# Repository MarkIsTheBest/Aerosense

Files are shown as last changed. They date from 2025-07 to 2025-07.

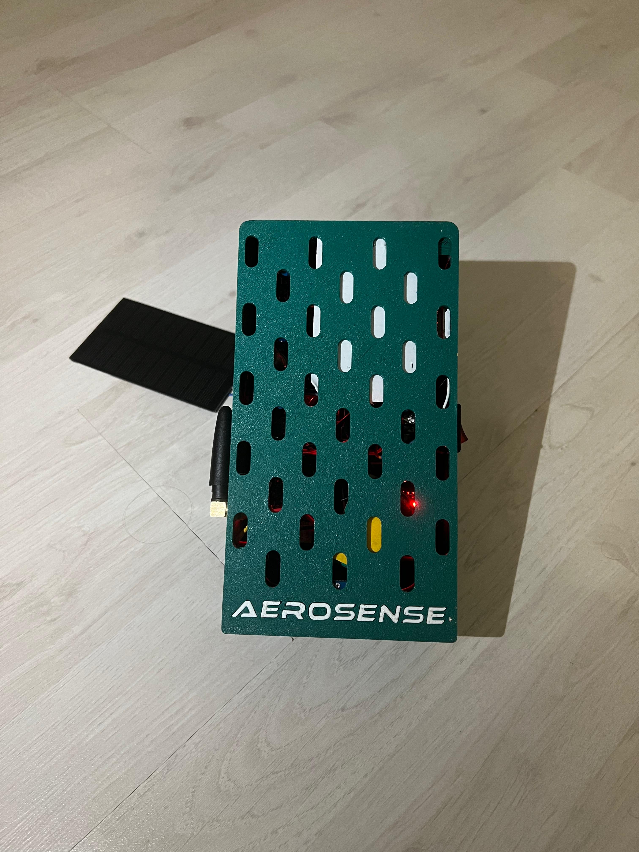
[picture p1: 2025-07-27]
Photos/Aerosense-7.jpg

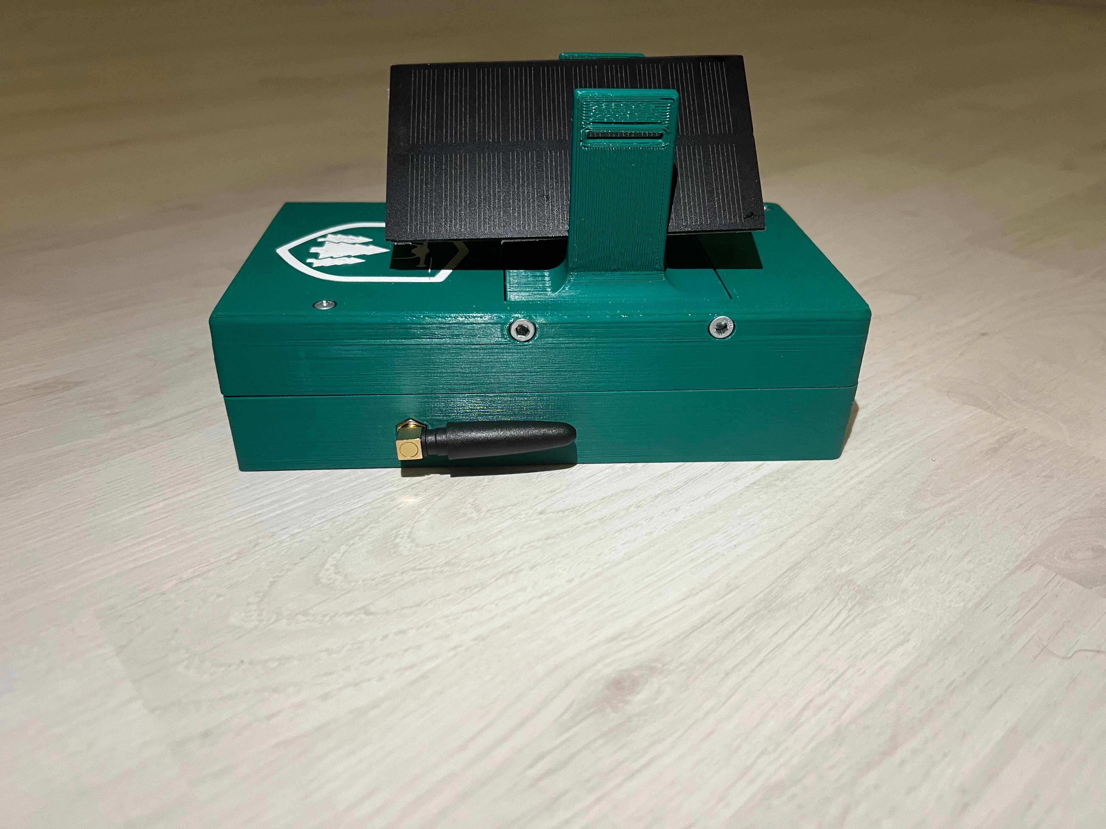
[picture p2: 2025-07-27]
Photos/Aerosense-8.jpg

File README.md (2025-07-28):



#### *Statie Meteo Mobila Autonoma, pentru culegerea datelor meteorologice, oricand si oriune.*

---

> [!NOTE]
> Acest ``README.md`` este strict dedicat partii technice al acestui proiect, pentru detalii mai generale, te rog visualizeaza prezentarea powerpoint, sau daca ai mai mult timp de citit, poti visualiza chiar si documentatia in intregime!

---

### Ierarhie pagina Github:
La ``Aerosense/Scripts/Drone.ino`` se gaseste codul Microcontroller-ului, acesta gestioneaza atat senzorii,
 cat si trimiterea lor pe webserver prin intermediului unei cartele SIM, iar simultan datele inregistrate sunt salvate
 pe o cartela MicroSD.

La ``Aerosense/Scripts/Webserver/`` se gasesc script-urile pentru Webserver, acestea includ:
- ``server.js`` (functionalitatea principala a server-ului prin intermediul Node.js)
- ``index.html`` (codul de baza a front-end-ului)
- ``style.css`` (stilistica front-end)

La ``Aerosense/3DModels/`` se gaseste modelul 3d al carcasei printate, care faciliteaza locuinta intregului sistem. Acest model se gaseste in mai multe format-uri pentru a usura uzul acestora. (Fusion360)

La ``Aerosense/Datasheets/`` se gasesc documente specifice a diverselor parti furnizate extern al sistemului nostru, cum ar fi de exemplu: baterie ce noi o folosim.

La ``Aerosense/Documentation/`` se gaseste atat documentatia cat si o prezentare powerpoint, pentru a usura intelegerea proiectului/sistemului, fiind scrisa la un mod mai general decat acest ``README.md`` care este strict technic:
- ``Aerosense Documentation.pdf`` (asa numita documentatie de 12 pagini)
- ``Aerosense Presentation.pptx`` (prezentare powerpoint generala)

La ``Aerosense/Photos/`` se gasesc diverse poze, capturand infatisarea sistemului, atat pe dinafara cat si pe dinauntru. Aceste poze va pot ajuta in vizualizaera sistemului.

La ``Aerosense/Schematics/`` se gaseste schematica circuitului electric facut in KiCad. Aceasta schematica nu face posibila doar visualizarea conexiuniilor electrice intre diferitii senzori, ci si a sistemului de alimentare. Urmarind aceasta schematica, proiectul poate fii facut mult mai mic prin intermediul, unui PCB presonalizat.

La ``Aerosense/Identity/`` se gaseste identitatea produsului, adica logo-ul si titlul acestuia, ambele pot fii gasite si pe carcasa sistemului.

-----

# Hardware:

### Componentele electronice de baza:
 1. #### Circuit Principal:
    * Microprocessor | Arduino Nano (USB C)
    - Senzor temperatura, presiune si umiditate | BME280
    - Busola/Magnetometru | QMC5883L
    - Senzor analogic de gaz si fum | MQ-7
    - Senzor analogic de oxid de carbon (CO) | MQ-5
    - Modul accelerometru + airoscop | MPU6050
    - Modul cartela SIM GSM + GPRS (+ Antena + SIM orange prepay) | SIM800LV2 EVB 
    - Senzor calitatea aerului | SGP30
    - Modul GPS (+ Antena) | NEO6MV3
    - Modul MicroSD Card (+ MicroSDHD Card 32GB)

2. #### Circuit Alimentare:
   - Acumulator Li-Ion 3.7V (MAX 4.2) 3350mAh | Samsung INR18650-25E
   - Panou Solar 5V 1W | YX-107X61
   - Modul Incarcare solara acumulator 3.7V | MPPT
   - Voltmetru (incarcatura acumulator)
   - Intrerupator (oprirea circuitului)
   - Ridicator de tensiune (3.7V -> 5V) 5A | XL6019
  
### Echipament utilizat:
| Tools | Manufacturer |
| --- | --- |
| `Ciocan de lipit (380C)` | `WCD` |
| `Ciocan de lipid (280C)` | `Dedeman` | 
| `Pistol Termic (380C)` | `WCD` |
| `Cositor SWCU 1/17 227C (fara plumb)` | `Dedeman` |
| `Sursa programabila 161,2W (5.2A)` | `WAPTEK` |
| `Imprimanta 3D Ender 3 V3 KE` | `Creality` |
| `+ Alte scule si unelte gasite` | `Acasa` |

-----

# Software:

### Librarii Folosite:

 1. #### Arduino:
    * ``SoftwareSerial.h`` (pentru a putea folosii oricare pini ca si TX/RX)
    * ``QMC5883LCompass.h`` (pentru gestionarea usoara si eficienta a busolei)
    * ``TinyGPSPlus.h`` (pentru interpretarea datelor primite de la sateliti)
    * ``I2Cdev.h`` (pentru conectarea si usurinta uzual a protocolului I2C)
    * ``MPU6050.h`` (pentru calibrarea si utilizarea eficienta a IMU-ului)
    * ``Wire.h`` (pentru a putea folosi protocolul de transmitere I2C)
    * ``sSense-BMx280I2C.h`` (pentru a banaliza folosirea senzorului ambiental)
    * ``Adafruit_SGP30.h`` (pentru a banaliza folosirea senzorului de calitate a aerului)
      
 2. #### Webserver:
    * ``http`` (pentru a facilita crearea unui server http)
    * ``fs`` (pentru a gestiona fisiere cu Node.js)
    * ``path`` (pentru a gestiona adresele fisierelor)
    * ``mysql2 + promise`` (pentru a efectua conexiunea cu baza de date mySQL)
    * ``leaflet(API)`` (pentru a avea acces la harta lumii)
    * ``gemini(API)`` (pentru a explica datele complicate utilizatorilor "non-experti")

### Baza de Date: MySQL

Pentru a stoca în mod persistent datele primite de la dronă, sistemul utilizează o bază de date ``MySQL``. Serverul ``Node.js`` acționează ca o punte de legătură între microcontroler și baza de date.
Conectarea la Baza de Date: Scriptul ``server.js`` folosește librăria ``mysql2/promise`` pentru a se conecta la serverul ``MySQL``. Detaliile de conectare (host, utilizator, parolă, numele bazei de date) sunt definite în obiectul ``dbConfig``.

#### Primirea și Inserarea Datelor:
1. Când microcontrolerul trimite date printr-o cerere ``POST`` la adresa ``/data``, serverul ``Node.js`` primește aceste informații în format ``JSON``.
2. Serverul adaugă un timestamp exact la momentul recepției pentru a asigura acuratețea temporală.
3. Datele sunt apoi inserate în tabelul ``drone_data`` din baza de date esp32_data folosind o interogare ``SQL`` de tip ``INSERT``. Utilizarea interogărilor parametrizate (cu ?) previne atacurile de tip ``SQL`` injection.
   
#### Livrarea Datelor către Front-End:
1. Pagina web (``index.html``) solicită datele de la server prin intermediul unei cereri ``GET`` la adresa ``/api/data``.
2. Serverul răspunde acestei cereri prin executarea unei interogări ``SQL`` de tip SELECT * FROM drone_data, extrăgând toate înregistrările.
3. Datele extrase sunt trimise către front-end în format JSON, unde sunt apoi folosite pentru a popula graficele și harta ``Leaflet``.

### Software extern utilizat:
| Software Name | Download Link |
|---|---|
| `Arduino IDE` | [`https://www.arduino.cc/en/software/`](https://www.arduino.cc/en/software/) |
| `Visual Studio Code` | [`https://code.visualstudio.com/`](https://code.visualstudio.com/) |
| `Fusion360` | [`https://www.autodesk.com/products/fusion-360/personal`](https://www.autodesk.com/products/fusion-360/personal) |
| `Creality Print` | [`https://www.creality.com/pages/download-software`](https://www.creality.com/pages/download-software) |
| `KiCad` | [`https://www.kicad.org/download/windows/`](https://www.kicad.org/download/windows/) |
| `MySQL` | [`https://www.mysql.com`](https://www.mysql.com) |
| `Gemini Pro AI` | [`https://gemini.google.com/`](https://gemini.google.com/) |
| `Canva` | [`https://www.canva.com/`](https://www.canva.com/) |

-----

## Galerie Foto:

### Placa de baza a sistemului:


### Sistemul de alimentare a placii:


### Schematica completa a sistemului din KiCad:


### Webserver-ul dronei:


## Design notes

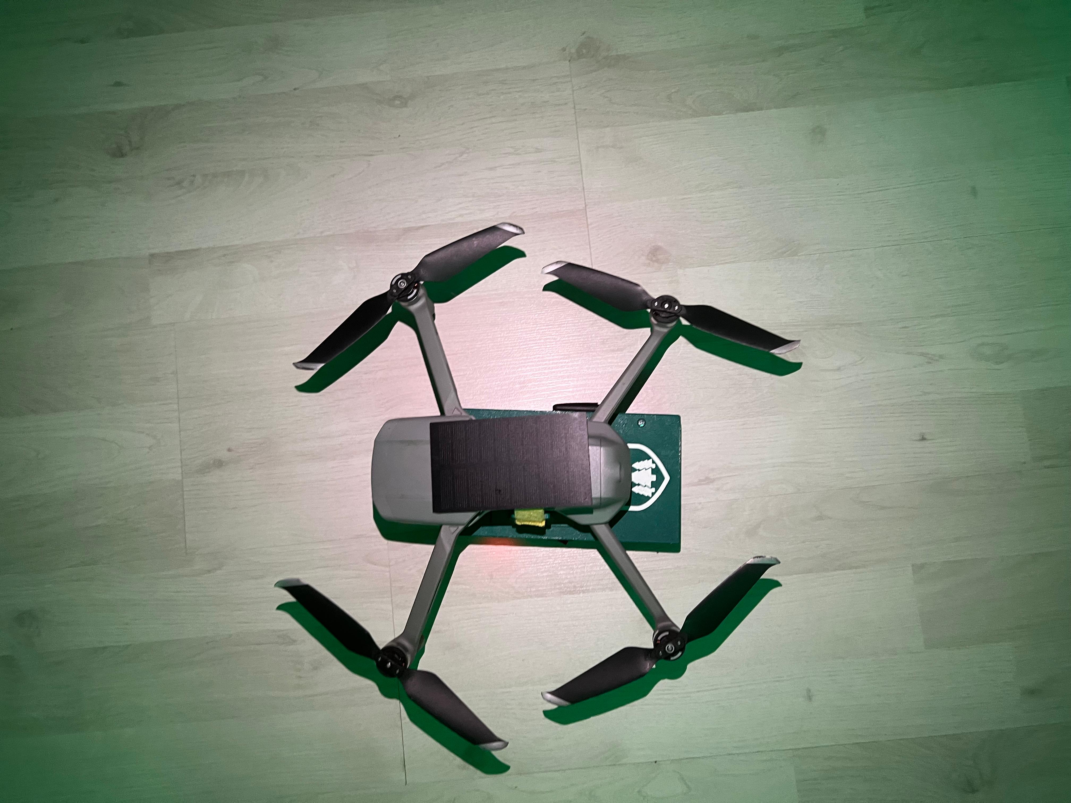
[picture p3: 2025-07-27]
Photos/Aerosense-5.jpg

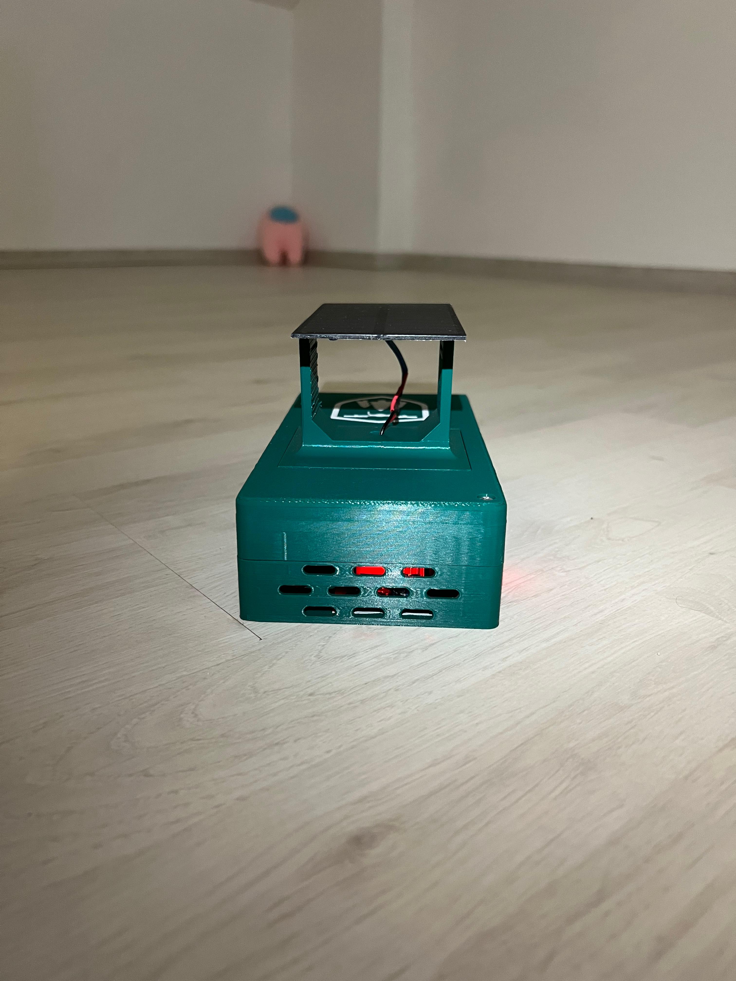
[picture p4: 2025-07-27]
Photos/Aerosense-2.jpg

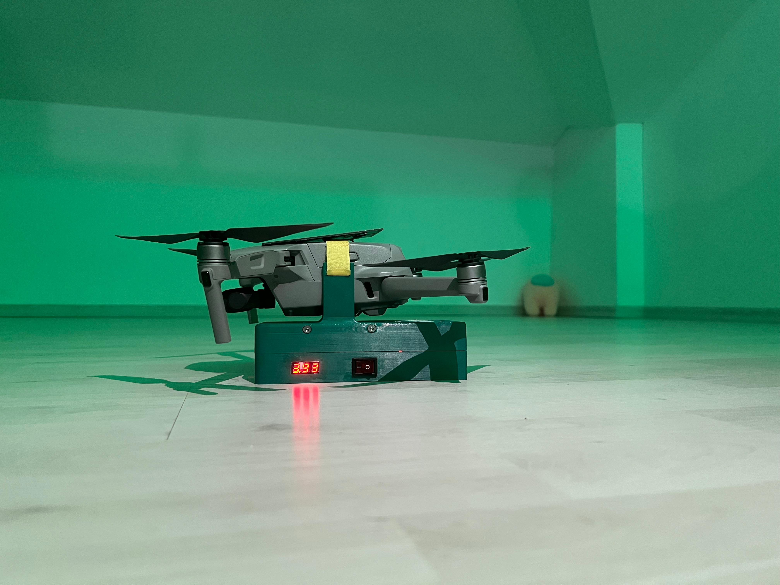
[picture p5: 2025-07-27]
Photos/Aerosense-4.jpg

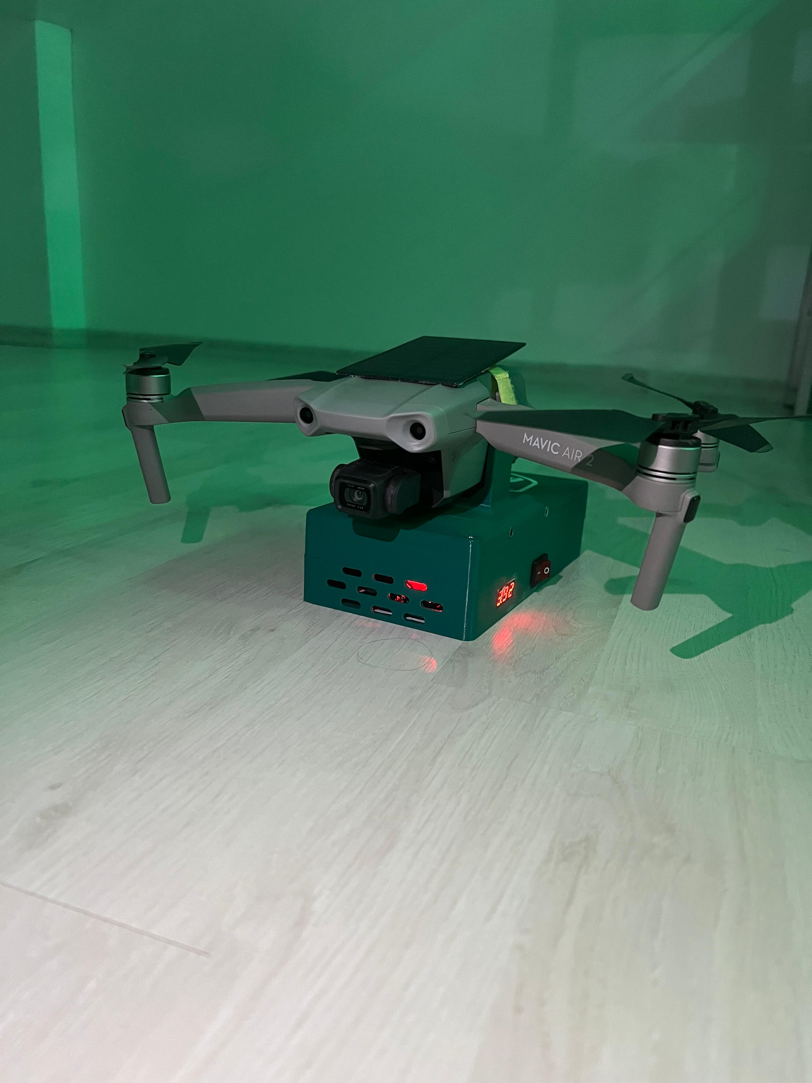
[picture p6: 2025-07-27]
Photos/Aerosense-1.jpg

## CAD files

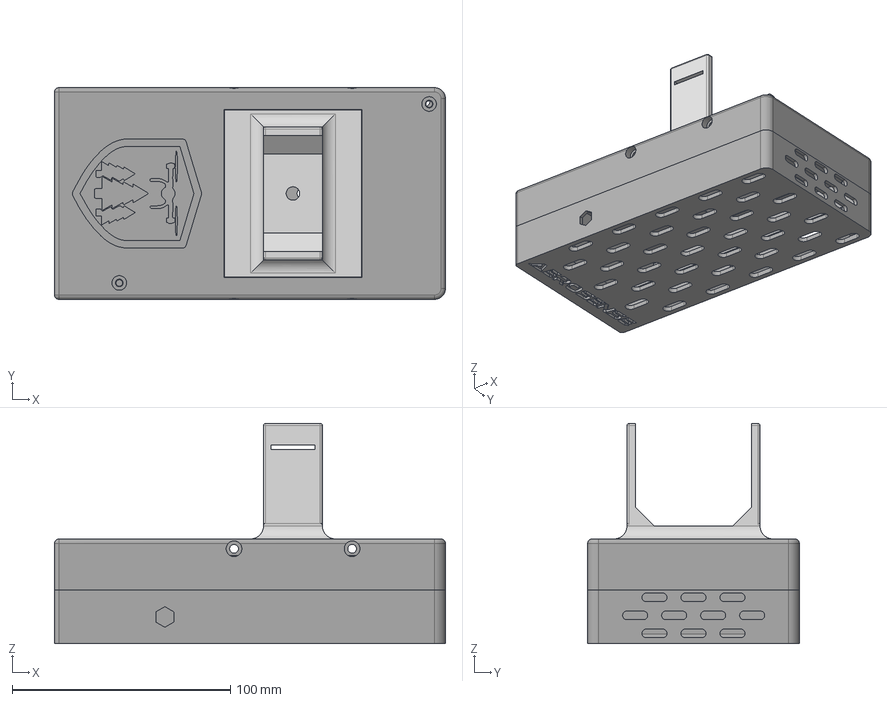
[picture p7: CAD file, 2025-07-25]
3DModels/Housing.step
179.2 x 97.0 x 101.0 mm
sketch
capac
fund (1)
scris

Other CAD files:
3DModels/Housing.3mf
3DModels/Housing.stl

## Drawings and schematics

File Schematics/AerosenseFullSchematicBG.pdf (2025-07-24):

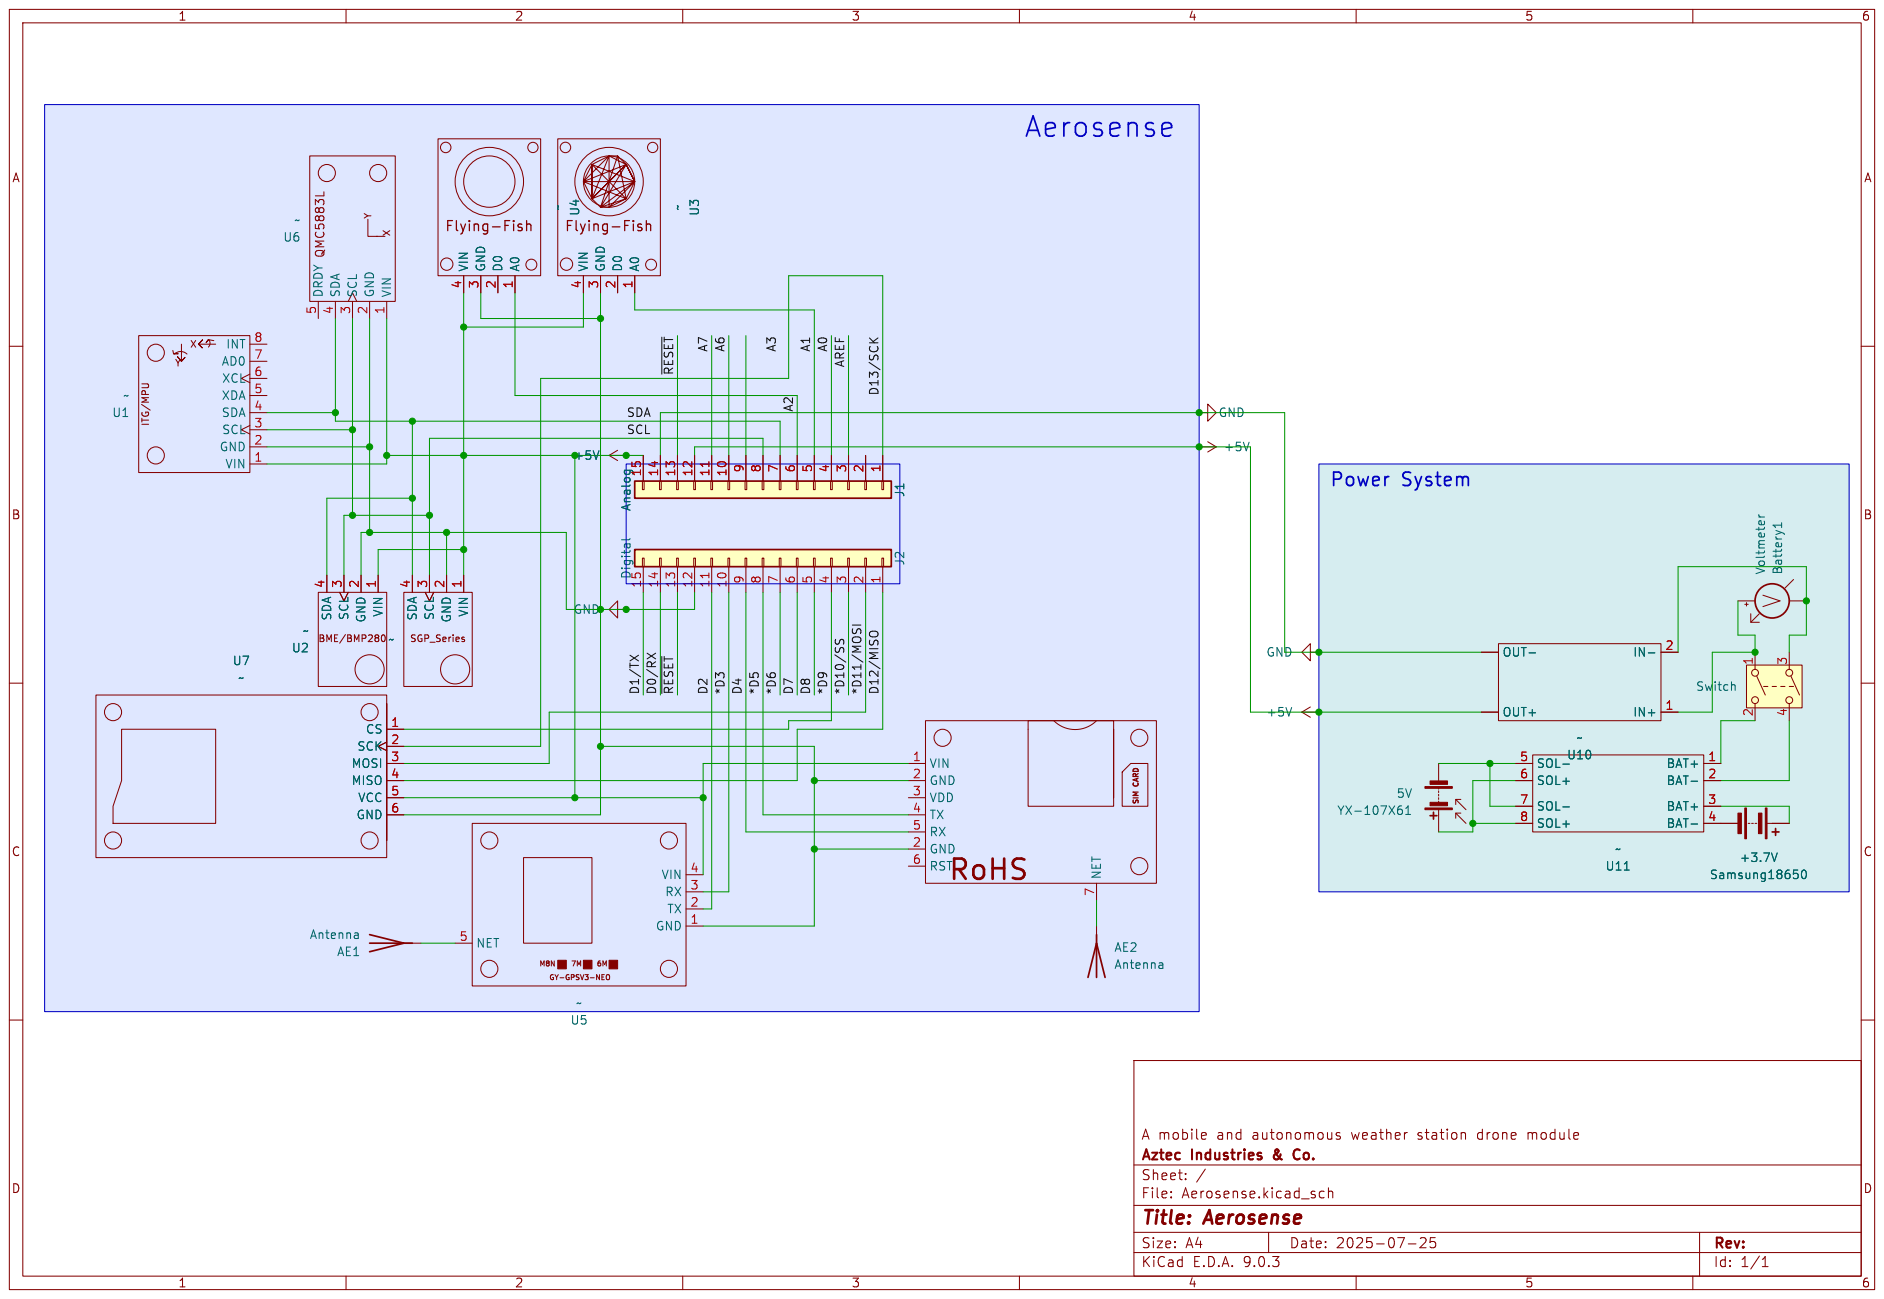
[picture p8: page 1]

4 U7~ CS 1 SCK 2 MOSI 3 MISO 4 VCC 5 GND 6~ VIN

1151413121110 J2 Digital A7 D1/TX D0/RX D2 D4 *D5 *D6 SCL ~{RESET} *D9 *D11/MOSI SDA D8 *D10/SS D12/MISO D13/SCK A2 A0 AREF *D3 D7 ~{RESET} A6A3A1

4 ~ BAT- 4 BAT+ 3 BAT- 2 BAT+ 1 SOL+ 8 SOL- 7 SOL+ 6 SOL- 5 U11~ AE2 Antenna RoHS SIM CARDVIN 1 GND 2 VDD 3 TX 4 RX 5 GND 2 RST 6 NET

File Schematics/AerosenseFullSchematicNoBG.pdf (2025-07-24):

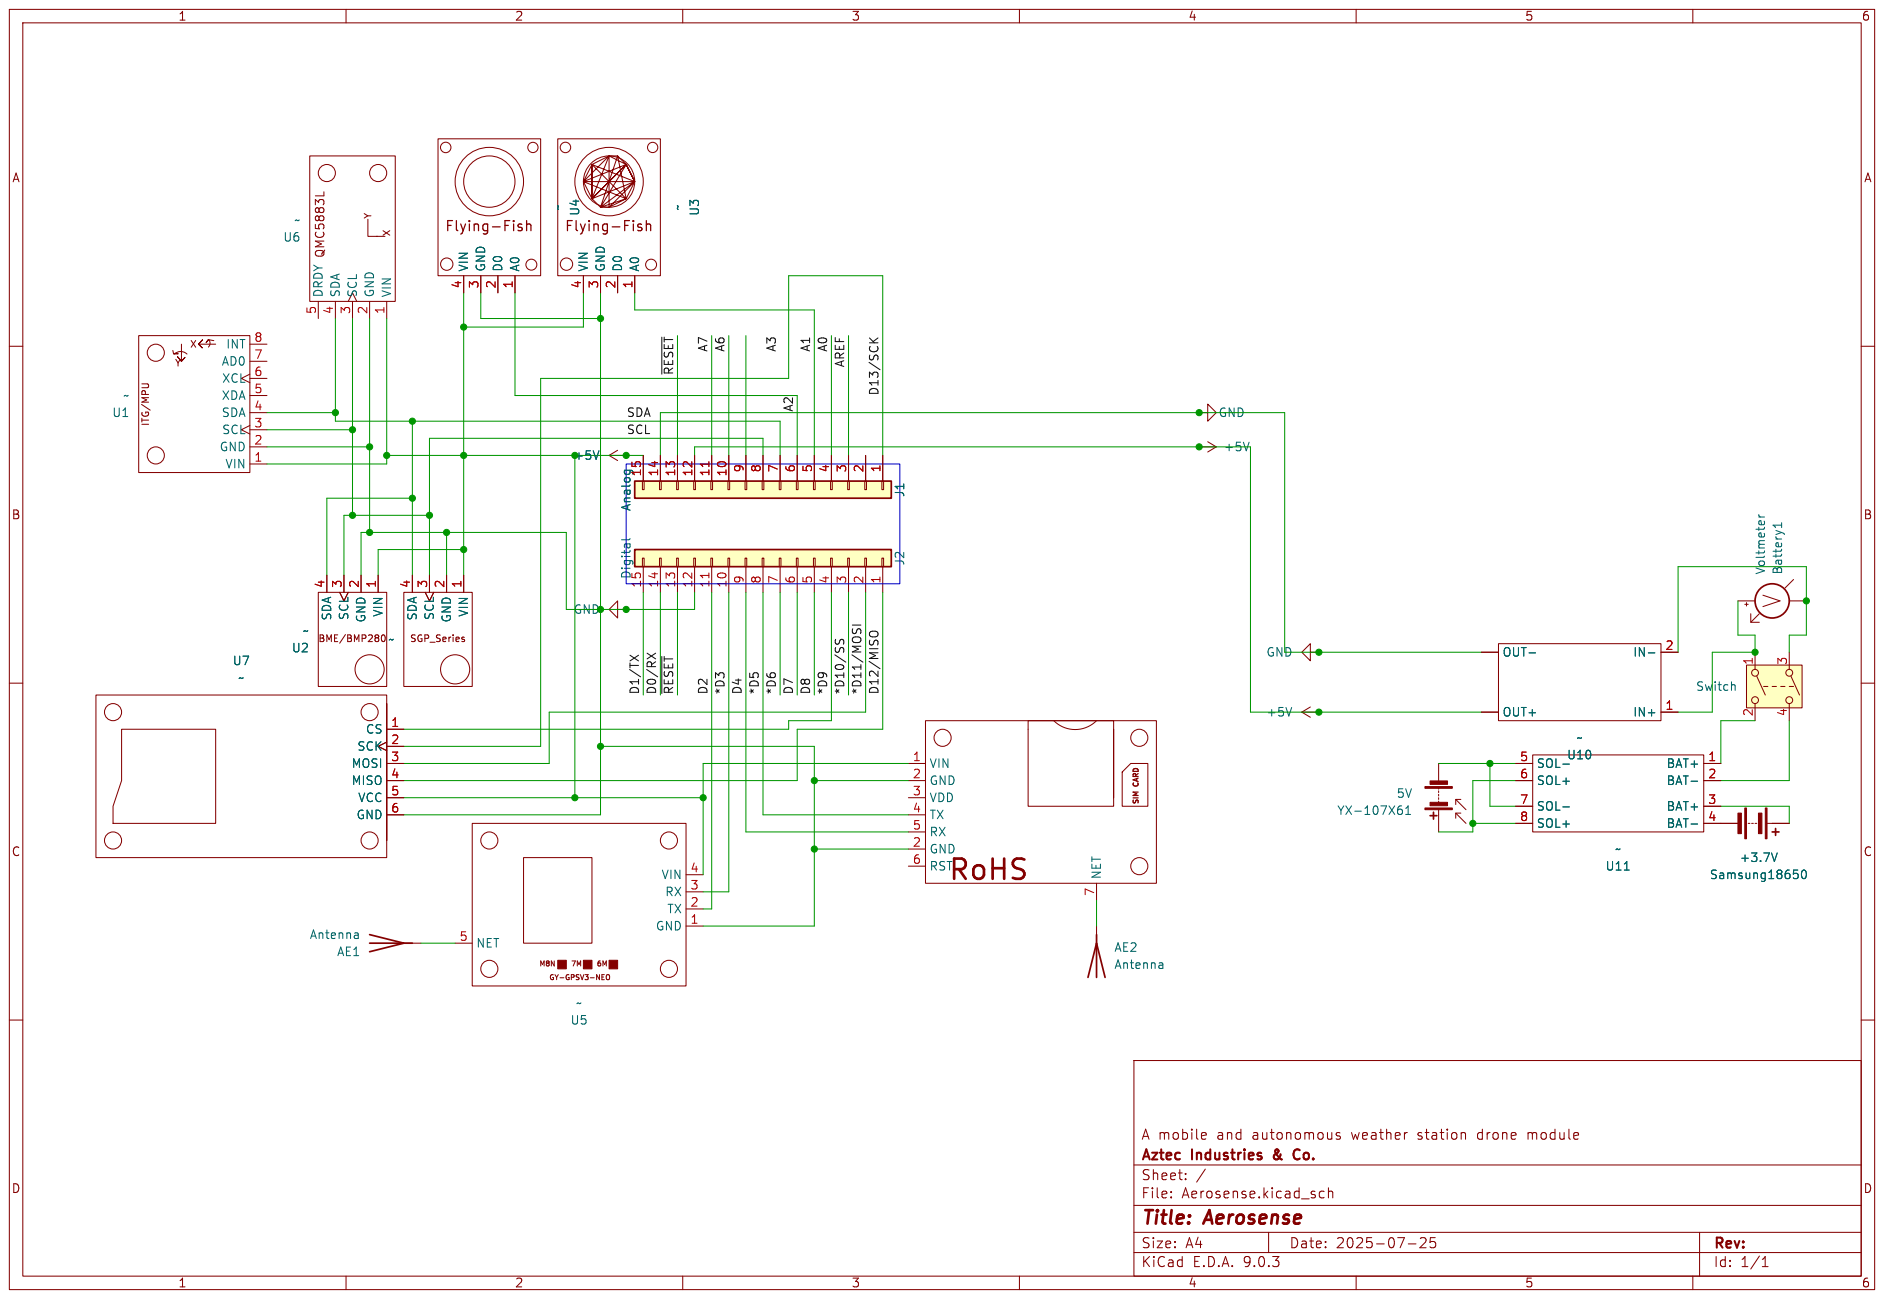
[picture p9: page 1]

4 U7~ CS 1 SCK 2 MOSI 3 MISO 4 VCC 5 GND 6~ VIN

4 ~ BAT- 4 BAT+ 3 BAT- 2 BAT+ 1 SOL+ 8 SOL- 7 SOL+ 6 SOL- 5 U11~ RoHS SIM CARDVIN 1 GND 2 VDD 3 TX 4 RX 5 GND 2 RST 6 NET

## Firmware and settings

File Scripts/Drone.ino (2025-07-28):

#include <SoftwareSerial.h>
#include <QMC5883LCompass.h>
#include <TinyGPSPlus.h>
#include "I2Cdev.h"
#include "MPU6050.h"
#include <Wire.h>
#include <Adafruit_BME280.h>
#include <Adafruit_SGP30.h>

const char APN[] = "net";
const char SERVER_IP[] = "62.231.112.115";
const char SERVER_PORT[] = "25565";

const int SIM800_RX_PIN = 4;
const int SIM800_TX_PIN = 5;
const int GAS_SENSOR_MQ5_PIN = A1;
const int GAS_SENSOR_MQ7_PIN = A2;
const int GPS_RX_PIN = 3;
const int GPS_TX_PIN = 2;
const uint32_t GPS_BAUD = 9600;
const float ACCEL_SCALE_FACTOR = 16384.0;
const float GRAVITY_MS2 = 9.81;

SoftwareSerial sim800l(SIM800_RX_PIN, SIM800_TX_PIN);
QMC5883LCompass compass;
TinyGPSPlus gps;
SoftwareSerial gpsSerial(GPS_RX_PIN, GPS_TX_PIN);
MPU6050 mpu;
Adafruit_BME280 bme; // I2C
Adafruit_SGP30 sgp;

char compassDirection[4];
int gasAnalogValue;
int coAnalogValue;
float gpsLatitude = 0.0;
float gpsLongitude = 0.0;
float gpsAltitude = 0.0;
float gpsSpeed = 0.0;
uint32_t sats = 0;
float accelX, accelY, accelZ;
float temperature, humidity, pressure;
uint16_t tvocLevel, co2Level;

unsigned long lastSendTime = 0;
const long sendInterval = 5000;

void setup() {
    Serial.begin(9600);
    sim800l.begin(9600);
    gpsSerial.begin(GPS_BAUD);

    Wire.begin();
    Wire.setClock(400000);

    Serial.println(F("--- Universal Sensor & GPRS Initializer ---"));
    delay(1000);

    initializeSensors();
    initializeGPRS();

    Serial.println(F("\n--- Setup complete. Starting main loop. ---\n"));
    lastSendTime = millis();
}

void loop() {
    gpsSerial.listen();
    
    while (gpsSerial.available() > 0) {
        gps.encode(gpsSerial.read());
    }

    if (millis() - lastSendTime >= sendInterval) {
        lastSendTime = millis();

        Serial.println(F("\n========================================"));
        Serial.println(F("Interval reached. Reading sensors and sending data..."));

        readAllSensors();
        sendData();

        Serial.println(F("========================================"));
    }
}

void readAllSensors() {
    Serial.println(F("--- Reading all sensor data... ---"));
    if (gps.location.isUpdated()) {
        gpsLatitude = gps.location.lat();
        gpsLongitude = gps.location.lng();
    }
    if (gps.altitude.isUpdated()) gpsAltitude = gps.altitude.meters();
    if (gps.speed.isUpdated()) gpsSpeed = gps.speed.kmph();
    if (gps.satellites.isUpdated()) sats = gps.satellites.value();

    compass.read();
    compass.getDirection(compassDirection, compass.getAzimuth());

    gasAnalogValue = analogRead(GAS_SENSOR_MQ5_PIN);
    coAnalogValue = analogRead(GAS_SENSOR_MQ7_PIN);

    int16_t raw_ax, raw_ay, raw_az;
    mpu.getAcceleration(&raw_ax, &raw_ay, &raw_az);
    accelX = (raw_ax / ACCEL_SCALE_FACTOR) * GRAVITY_MS2;
    accelY = (raw_ay / ACCEL_SCALE_FACTOR) * GRAVITY_MS2;
    accelZ = (raw_az / ACCEL_SCALE_FACTOR) * GRAVITY_MS2;

    temperature = bme.readTemperature();
    humidity = bme.readHumidity();
    pressure = bme.readPressure(); // This returns pressure in Pascals (Pa)
    if (humidity > 0) sgp.setHumidity(getAbsoluteHumidity(temperature, humidity));
    if (sgp.IAQmeasure()) {
        tvocLevel = sgp.TVOC;
        co2Level = sgp.eCO2;
    }
    printData();
}

void sendData() {
    sendHttpPost();
}

void initializeSensors() {
    Serial.println(F("--- Initializing Sensors ---"));
    Serial.print(F("QMC5883L... "));
    compass.init();
    Serial.println(F("Done."));
    Serial.print(F("MPU6050... "));
    mpu.initialize();
    if (mpu.testConnection()) {
        Serial.println(F("OK. Setting offsets..."));
        mpu.setXAccelOffset(1690); mpu.setYAccelOffset(870); mpu.setZAccelOffset(4640);
        mpu.setXGyroOffset(-46); mpu.setYGyroOffset(68); mpu.setZGyroOffset(88);
    } else {
        Serial.println(F("Failed."));
    }
    Serial.print(F("BME280... "));
    if (!bme.begin(0x76)) Serial.println(F("Failed. Check wiring or I2C address!"));
    else Serial.println(F("Done."));
    Serial.print(F("SGP30... "));
    if (!sgp.begin()) Serial.println(F("Failed."));
    else Serial.println(F("Done."));
    Serial.println(F("--- Sensor Initialization Complete ---"));
}

void initializeGPRS() {
    sim800l.listen();
    Serial.println(F("--- Initializing SIM800L Module ---"));
    delay(3000);
    if (!checkModule()) {
        Serial.println(F("FATAL: SIM800L module not responding. Halting."));
        while (1);
    }
    sendATCommand(F("AT+HTTPTERM"), F("OK"), 5000);
    sendATCommand(F("AT+SAPBR=0,1"), F("OK"), 5000);
    setupGPRS();
}

unsigned int countDigits(int number) {
  if (number < 0) return countDigits(-number) + 1;
  if (number < 10) return 1;
  if (number < 100) return 2;
  if (number < 1000) return 3;
  if (number < 10000) return 4;
  return 5;
}

bool expectResponse(const __FlashStringHelper* ack, unsigned int timeout) {
    String response = "";
    response.reserve(64);
    long int startTime = millis();
    bool ackFound = false;
    while ((millis() - startTime) < timeout) {
        while (sim800l.available()) {
            response += (char)sim800l.read();
        }
        if (response.indexOf(ack) != -1) {
            ackFound = true;
            break;
        }
    }
    Serial.print(F("<<< Response: "));
    Serial.println(response);
    return ackFound;
}

bool sendATCommand(const __FlashStringHelper* cmd, const __FlashStringHelper* ack, unsigned int timeout) {
    Serial.print(F(">>> AT: "));
    Serial.println(cmd);
    sim800l.println(cmd);
    return expectResponse(ack, timeout);
}

bool checkModule() {
    return sendATCommand(F("AT"), F("OK"), 2000);
}

void setupGPRS() {
    Serial.println(F("--- Configuring GPRS ---"));
    sendATCommand(F("AT+CREG?"), F("+CREG: 0,1"), 10000);
    sendATCommand(F("AT+CGATT=1"), F("OK"), 5000);
    sim800l.print(F("AT+SAPBR=3,1,\"CONTYPE\",\"GPRS\"\r\n"));
    expectResponse(F("OK"), 2000);
    sim800l.print(F("AT+SAPBR=3,1,\"APN\",\""));
    sim800l.print(APN);
    sim800l.print(F("\"\r\n"));
    expectResponse(F("OK"), 2000);
    sendATCommand(F("AT+SAPBR=1,1"), F("OK"), 20000);
    sendATCommand(F("AT+SAPBR=2,1"), F("+SAPBR:"), 5000);
    Serial.println(F("--- GPRS Configuration Complete ---"));
}

void sendHttpPost() {
    sim800l.listen();
    Serial.println(F("--- Starting HTTP POST ---"));
    if (!sendATCommand(F("AT+HTTPINIT"), F("OK"), 5000)) return;

    sim800l.print(F("AT+HTTPPARA=\"URL\",\"http://"));
    sim800l.print(SERVER_IP);
    sim800l.print(F(":"));
    sim800l.print(SERVER_PORT);
    sim800l.print(F("/data\"\r\n"));
    if (!expectResponse(F("OK"), 2000)) return;

    sendATCommand(F("AT+HTTPPARA=\"CONTENT\",\"application/json\""), F("OK"), 2000);

    char tempBuffer[12];
    int jsonLength = 0;
    jsonLength += strlen_P(PSTR("{\"path\":1,\"timestamp\":\"2025-01-01 00:00:00\",\"longitude\":,\"latitude\":,\"temperature\":,\"humidity\":,\"pressure\":,\"CO2level\":,\"TVOClevel\":,\"imuXaccel\":,\"imuYaccel\":,\"imuZaccel\":,\"COlevel\":,\"Gaslevel\":,\"altitude\":,\"speed\":,\"sats\":,\"direction\":\"\"}"));
    jsonLength += strlen(dtostrf(gpsLongitude, 0, 6, tempBuffer));
    jsonLength += strlen(dtostrf(gpsLatitude, 0, 6, tempBuffer));
    jsonLength += strlen(dtostrf(temperature, 0, 2, tempBuffer));
    jsonLength += strlen(dtostrf(humidity, 0, 2, tempBuffer));
    jsonLength += strlen(dtostrf(pressure, 0, 0, tempBuffer));
    jsonLength += countDigits(co2Level);
    jsonLength += countDigits(tvocLevel);
    jsonLength += strlen(dtostrf(accelX, 0, 2, tempBuffer));
    jsonLength += strlen(dtostrf(accelY, 0, 2, tempBuffer));
    jsonLength += strlen(dtostrf(accelZ, 0, 2, tempBuffer));
    jsonLength += countDigits(coAnalogValue);
    jsonLength += countDigits(gasAnalogValue);
    jsonLength += strlen(dtostrf(gpsAltitude, 0, 2, tempBuffer));
    jsonLength += strlen(dtostrf(gpsSpeed, 0, 2, tempBuffer));
    jsonLength += countDigits(sats);
    jsonLength += strlen(compassDirection);

    sim800l.print(F("AT+HTTPDATA="));
    sim800l.print(jsonLength);
    sim800l.println(F(",10000"));

    if (expectResponse(F("DOWNLOAD"), 5000)) {
        Serial.println(F(">>> Sending payload piece by piece..."));
        sim800l.print(F("{\"path\":1,\"timestamp\":\"2025-01-01 00:00:00\""));
        sim800l.print(F(",\"longitude\":")); sim800l.print(dtostrf(gpsLongitude, 0, 6, tempBuffer));
        sim800l.print(F(",\"latitude\":")); sim800l.print(dtostrf(gpsLatitude, 0, 6, tempBuffer));
        sim800l.print(F(",\"temperature\":")); sim800l.print(dtostrf(temperature, 0, 2, tempBuffer));
        sim800l.print(F(",\"humidity\":")); sim800l.print(dtostrf(humidity, 0, 2, tempBuffer));
        sim800l.print(F(",\"pressure\":")); sim800l.print(dtostrf(pressure, 0, 0, tempBuffer));
        sim800l.print(F(",\"CO2level\":")); sim800l.print(co2Level);
        sim800l.print(F(",\"TVOClevel\":")); sim800l.print(tvocLevel);
        sim800l.print(F(",\"imuXaccel\":")); sim800l.print(dtostrf(accelX, 0, 2, tempBuffer));
        sim800l.print(F(",\"imuYaccel\":")); sim800l.print(dtostrf(accelY, 0, 2, tempBuffer));
        sim800l.print(F(",\"imuZaccel\":")); sim800l.print(dtostrf(accelZ, 0, 2, tempBuffer));
        sim800l.print(F(",\"COlevel\":")); sim800l.print(coAnalogValue);
        sim800l.print(F(",\"Gaslevel\":")); sim800l.print(gasAnalogValue);
        sim800l.print(F(",\"altitude\":")); sim800l.print(dtostrf(gpsAltitude, 0, 2, tempBuffer));
        sim800l.print(F(",\"speed\":")); sim800l.print(dtostrf(gpsSpeed, 0, 2, tempBuffer));
        sim800l.print(F(",\"sats\":")); sim800l.print(sats);
        sim800l.print(F(",\"direction\":\"")); sim800l.print(compassDirection); sim800l.print(F("\""));
        sim800l.print(F("}"));
        sim800l.println();

        if (!expectResponse(F("OK"), 10000)) {
            Serial.println(F("Error: Payload send failed."));
        }
    } else {
        Serial.println(F("Error setting HTTP data."));
    }

    if (sendATCommand(F("AT+HTTPACTION=1"), F("+HTTPACTION: 1,201"), 20000)) {
        Serial.println(F("Success: POST sent, server returned 201 OK."));
    } else {
        Serial.println(F("Error: HTTP POST failed."));
    }

    sendATCommand(F("AT+HTTPREAD"), F("OK"), 5000);
    sendATCommand(F("AT+HTTPTERM"), F("OK"), 5000);
    Serial.println(F("--- HTTP POST Finished ---"));
}

void printData() {
    Serial.println(F("-------------------- SENSOR DATA --------------------"));
    Serial.print(F("Compass: ")); Serial.print(compassDirection);
    Serial.print(F("\t| Gas (MQ-5): ")); Serial.print(gasAnalogValue);
    Serial.print(F("\t| CO (MQ-7): ")); Serial.println(coAnalogValue);
    Serial.print(F("GPS: ")); Serial.print(gpsLatitude, 6); Serial.print(F(", ")); Serial.print(gpsLongitude, 6);
    Serial.print(F(" | Alt: ")); Serial.print(gpsAltitude);
    Serial.print(F(" m | Spd: ")); Serial.print(gpsSpeed);
    Serial.print(F(" km/h | Sats: ")); Serial.println(sats);
    Serial.print(F("IMU Accel (X/Y/Z): ")); Serial.print(accelX, 2); Serial.print(F(" / ")); Serial.print(accelY, 2); Serial.print(F(" / ")); Serial.print(accelZ, 2); Serial.println(F(" m/s^2"));
    Serial.print(F("Env: ")); Serial.print(temperature, 2); Serial.print(F(" C | ")); Serial.print(humidity, 2); Serial.print(F(" % | ")); Serial.print(pressure, 0); Serial.println(F(" Pa"));
    Serial.print(F("Air Quality: TVOC ")); Serial.print(tvocLevel); Serial.print(F(" ppb | eCO2 ")); Serial.print(co2Level); Serial.println(F(" ppm"));
    Serial.println(F("-----------------------------------------------------\n"));
}

uint32_t getAbsoluteHumidity(float temp, float hum) {
    const float absoluteHumidity = 216.7f * ((hum / 100.0f) * 6.112f * exp((17.62f * temp) / (243.12f + temp)) / (273.15f + temp));
    return static_cast<uint32_t>(1000.0f * absoluteHumidity);
}
